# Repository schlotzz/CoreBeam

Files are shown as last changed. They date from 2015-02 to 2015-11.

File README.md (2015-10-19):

CoreBeam Logo

CoreBeam is a low cost DIY laser cutter/engraver based on [CoreXY](http://corexy.com/) kinematics. Its size can be scaled easily to suit your requirements and without the need to reprint parts.

### CoreBeam Key Features
- low cost, entry-level solution
- easy to build and assemble with basic hobbyist tools
- workspace size can be increased easily

### What electronics/firmware have been used?
The machine is controlled by a [slightly modified](https://github.com/schlotzz/grbl) version 0.9i of [grbl](https://github.com/grbl/grbl) running on an Arduino Uno with grbl-shield, a custom hand-soldered MOSFET-PCB and a cheap current limiting circuit-board.

### Which software can I use?
Due to using grbl as firmware a wide range of software can be used with CoreBeam. For streaming g-code via USB both [Universal G-Code Sender](https://github.com/winder/Universal-G-Code-Sender) and [GrblController](https://github.com/zapmaker/GrblHoming) have been tested successfully. Designing vector-images and converting them into g-code is easy as pie with [InkScape](https://inkscape.org) and the [LaserEngraver](http://www.slackersdelight.com/instructables/laserengraver.zip) extension, a heavily modified version of [Gcodetools](http://www.cnc-club.ru/forum/viewtopic.php?f=15&p=101).

### What materials can be handled?
Using a 2W 445nm M140 blue laser diode, CoreBeam has been tested for working with the following materials:

| Material | Cut | Engrave |
| :--- | :---: | :---: |
| Paper (any color) | Yes | Yes |
| Cardboard (any color) | Yes | Yes |
| Corrugated cardboard | Yes | Yes |
| Foam rubber (Polyurathane) | Yes | Yes |
| Synthetic felt | Yes | Yes |
| Wood (<= 1mm) | Yes | Yes |
| Wood (> 1mm) | No | Yes |
| Leather (<= 3mm) | Yes | Yes |
| Self-adhesive foils | Yes | Yes |
| Acrylic | No | Yes |
| Metal | No | No |

### Safety warnings
A powerfull laser diode is **not a toy**. Focused laser beams can burn your skin and damage your eyes permanently if not used responsibly. Please do yourself a favor and always use suitable, **certified laser goggles** while working with your laser cutter/engraver.
I do recommend operating CoreBeam only in well ventilated areas and only on materials **not emitting toxic fumes**.

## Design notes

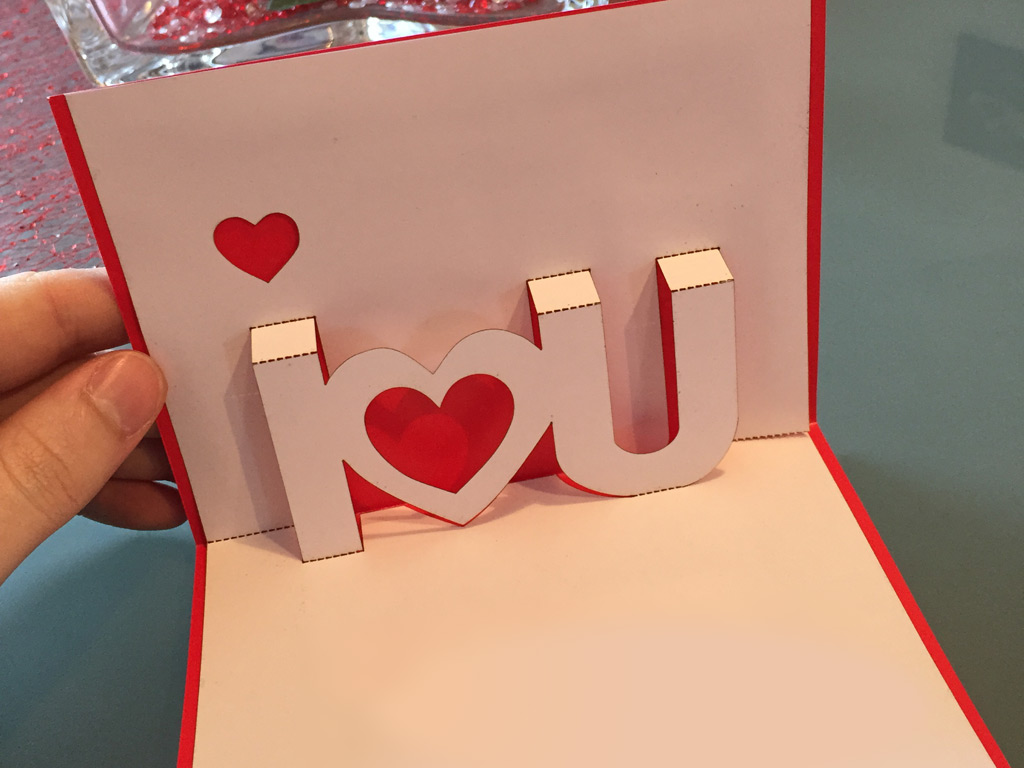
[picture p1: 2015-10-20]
media/materials/paper-cut.jpg

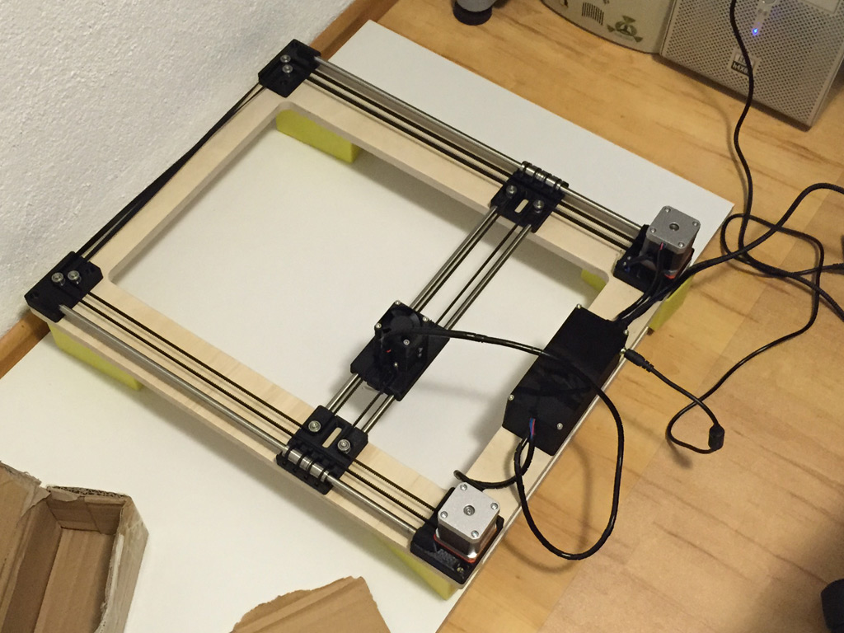
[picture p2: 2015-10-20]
media/buildlog/electronics-enclosed.jpg

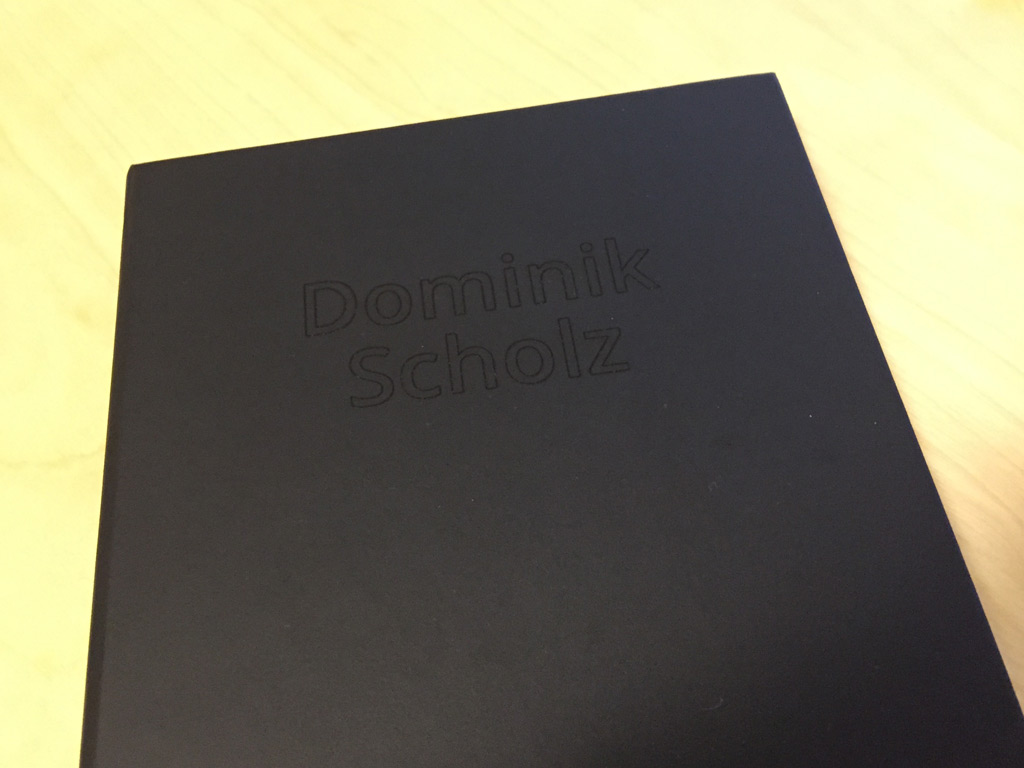
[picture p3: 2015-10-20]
media/materials/paper-book-engraved.jpg

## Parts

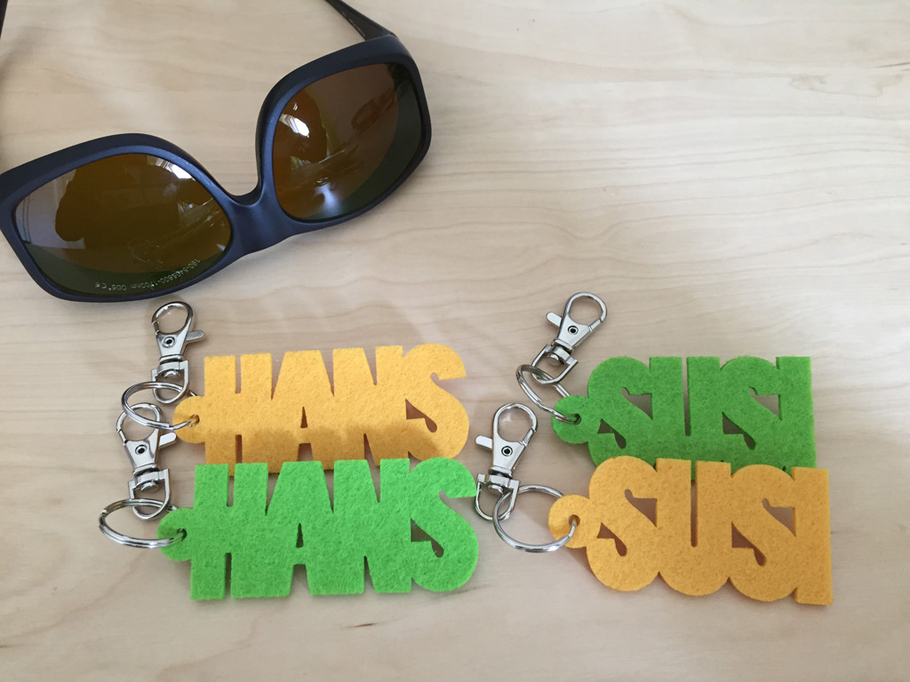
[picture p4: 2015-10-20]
media/materials/synthetic-felt-cut.jpg

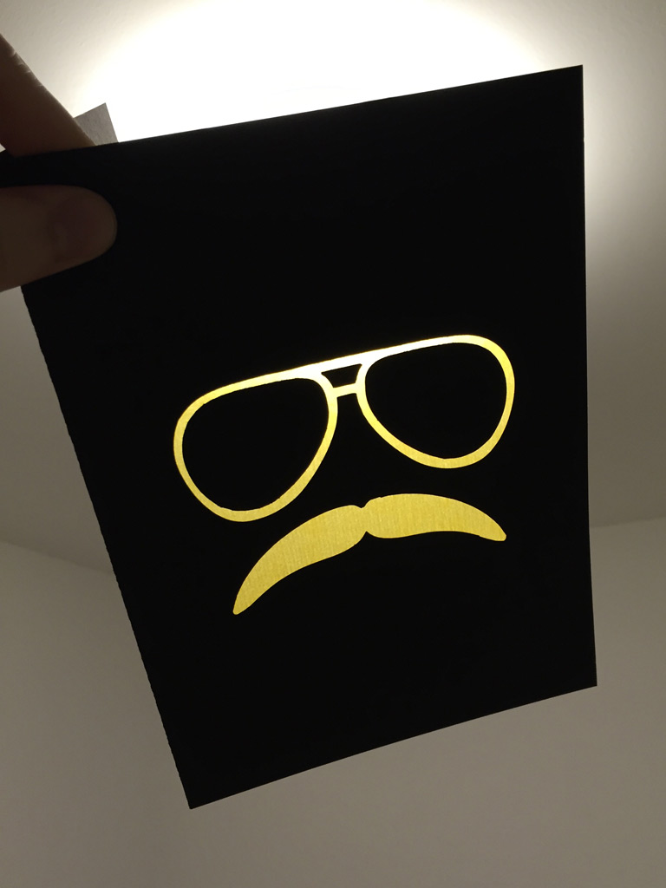
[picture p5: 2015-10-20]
media/materials/cardboard-cut.jpg

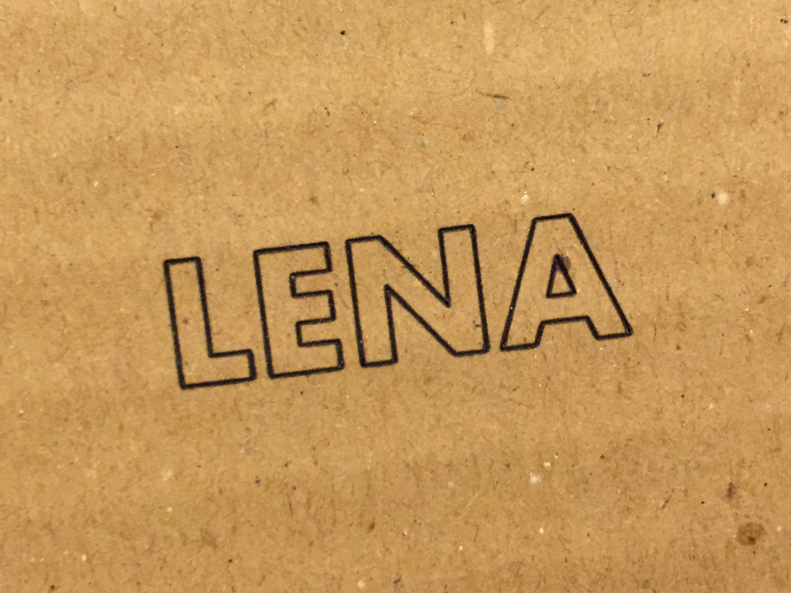
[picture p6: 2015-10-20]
media/materials/corrugated-cardboard-engraved.jpg

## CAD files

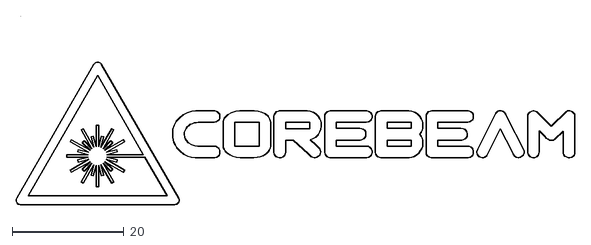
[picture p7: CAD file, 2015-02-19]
logo/corebeam.dxf
100.0 x 33.7

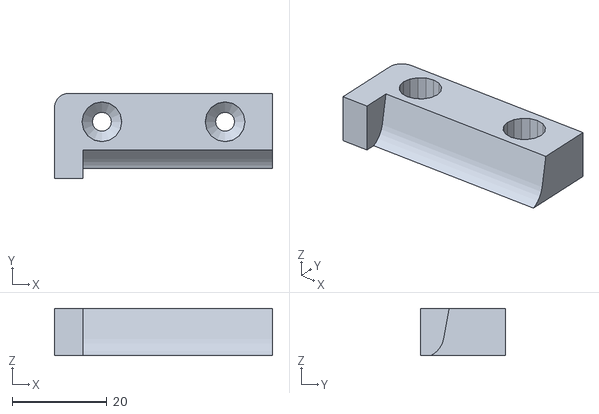
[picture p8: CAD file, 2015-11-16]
stl/pedestal-stopper.stl
46.0 x 18.0 x 10.0

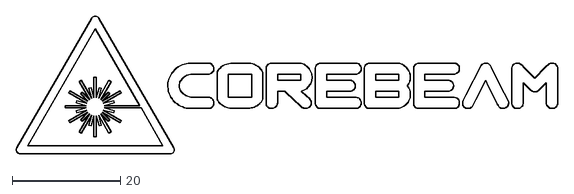
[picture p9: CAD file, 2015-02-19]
logo/corebeam-simplified-foreground.dxf
100.0 x 25.5

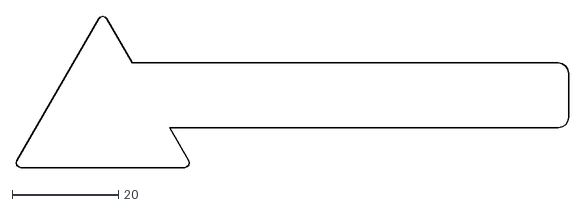
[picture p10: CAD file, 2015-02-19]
logo/corebeam-simplified-background.dxf
104.0 x 28.4

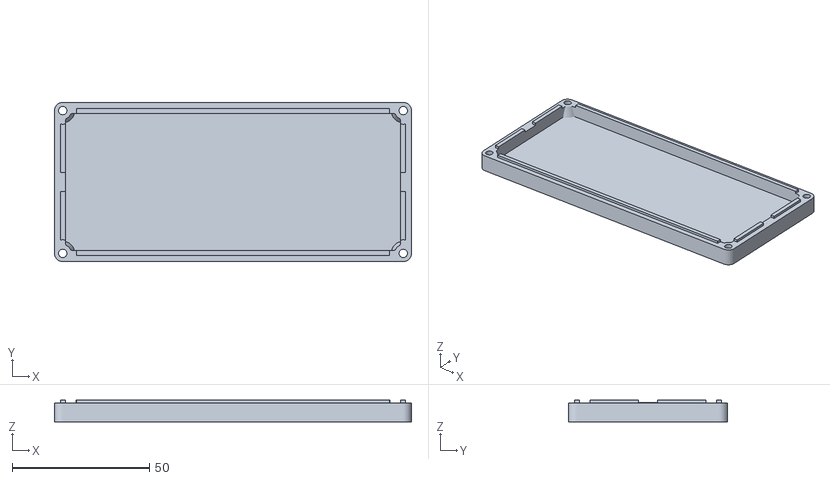
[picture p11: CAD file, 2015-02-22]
stl/electronics-case-lid.stl
130.0 x 58.0 x 8.00

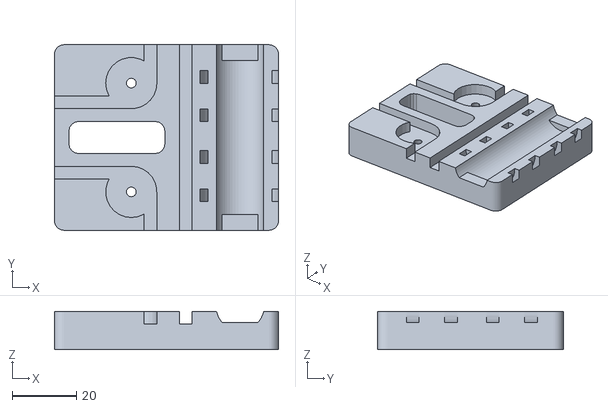
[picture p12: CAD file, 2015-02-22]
stl/stage-y.stl
70.0 x 58.0 x 12.0

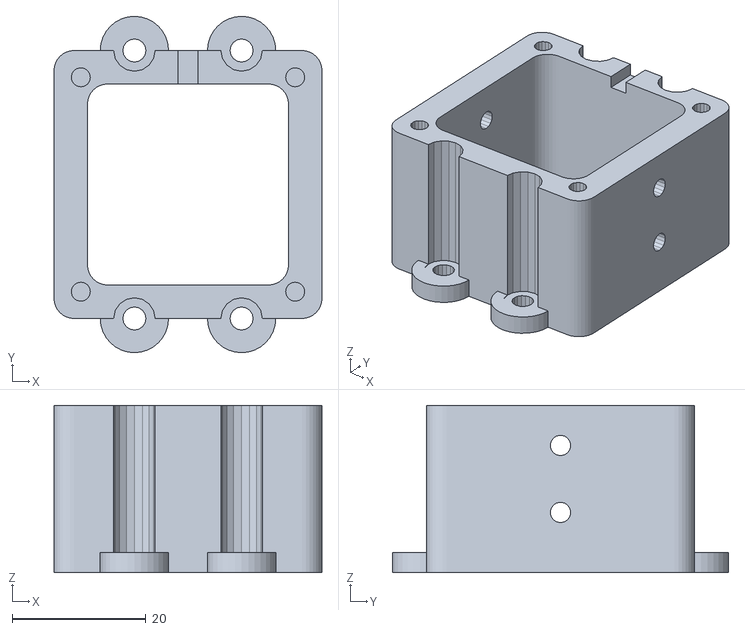
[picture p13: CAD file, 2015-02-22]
stl/laser-tower.stl
40.0 x 50.2 x 25.0

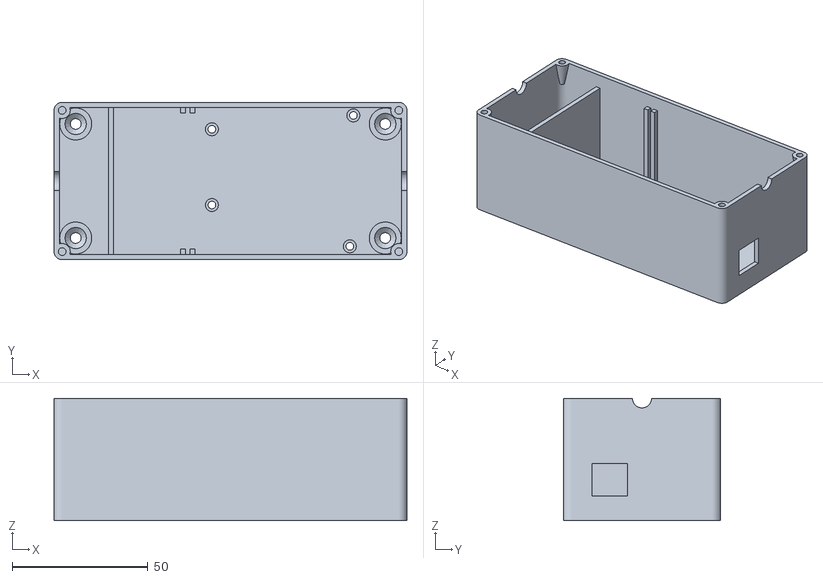
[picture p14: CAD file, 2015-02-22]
stl/electronics-case.stl
130.0 x 58.0 x 45.0

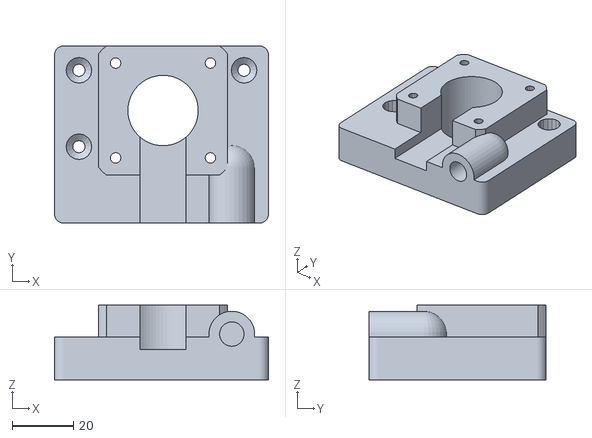
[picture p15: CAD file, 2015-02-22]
stl/stage-bottom.stl
70.0 x 58.0 x 24.5

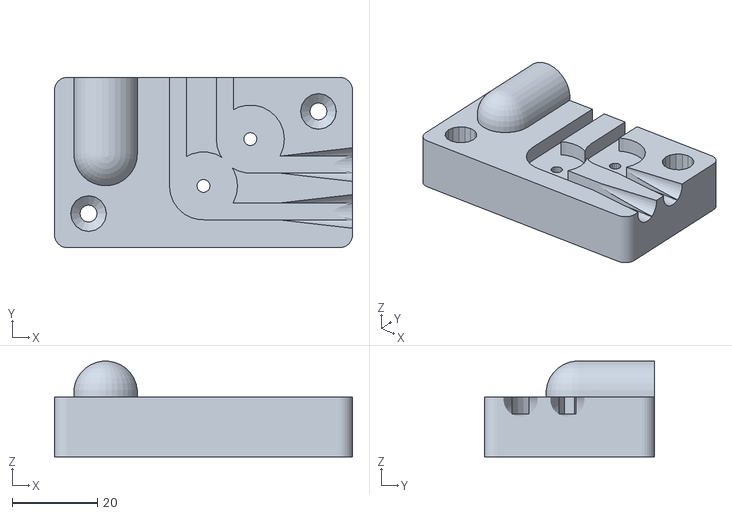
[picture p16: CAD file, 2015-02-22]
stl/stage-top-mirrored.stl
70.0 x 40.0 x 22.5

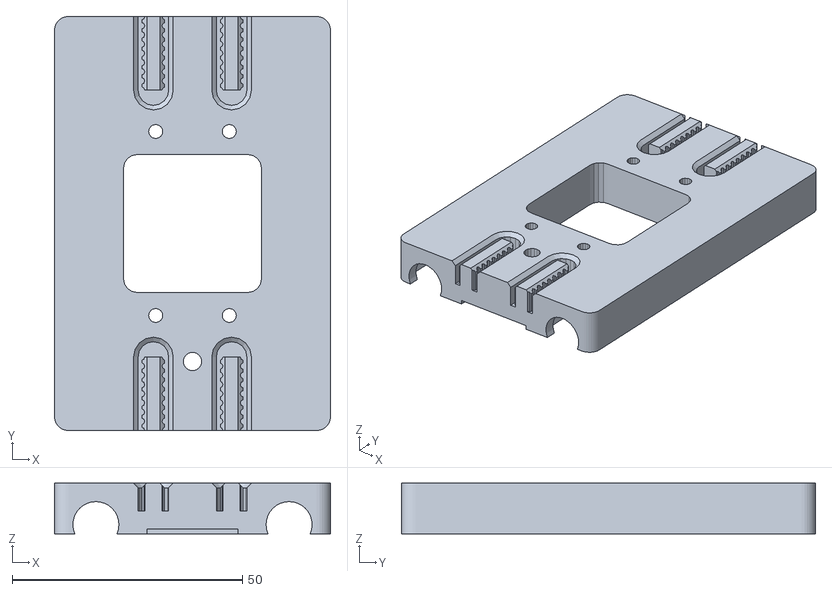
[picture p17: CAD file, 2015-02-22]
stl/stage-x.stl
60.0 x 90.0 x 11.0

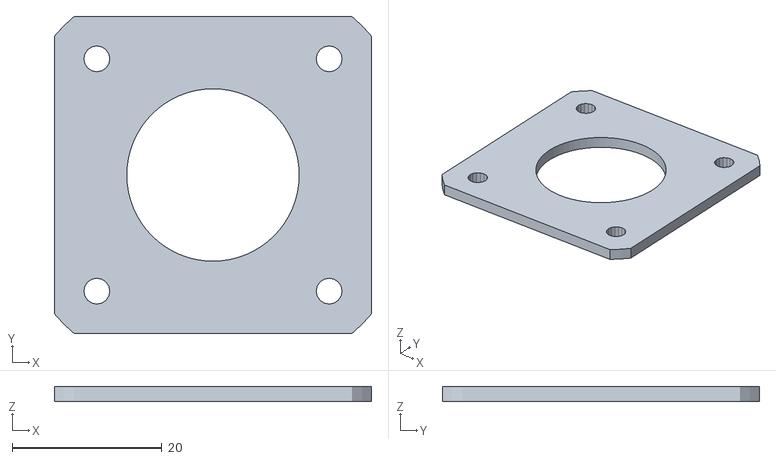
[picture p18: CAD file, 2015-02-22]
stl/motor-shim.stl
42.3 x 42.3 x 2.00

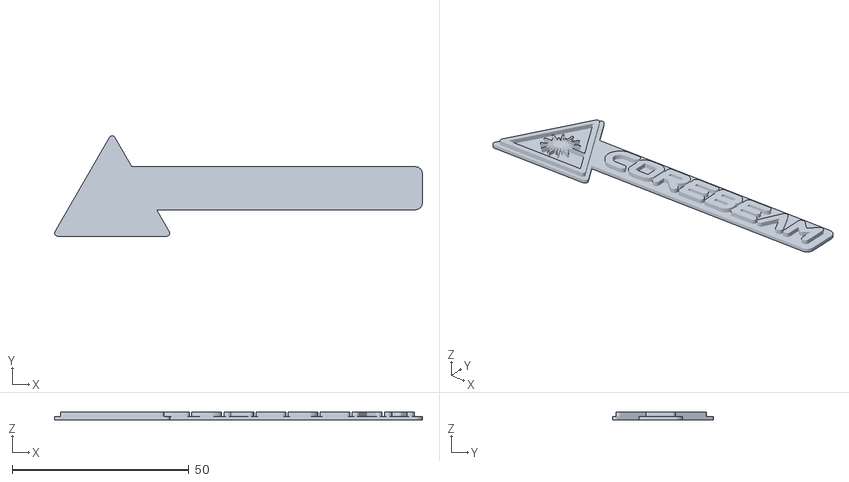
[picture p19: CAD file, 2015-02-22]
stl/corebeam-label.stl
104.0 x 28.4 x 2.25

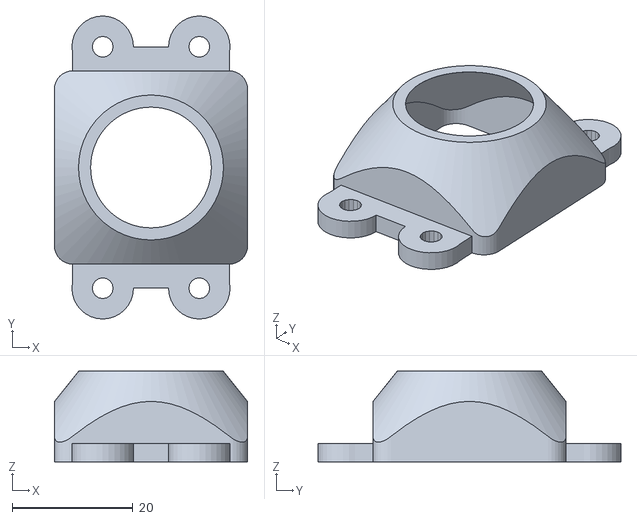
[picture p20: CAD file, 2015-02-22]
stl/laser-end-cap.stl
32.0 x 50.2 x 15.0

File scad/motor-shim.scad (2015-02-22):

// CoreBeam Laser Engraver
//
// Licence: CC BY-SA 3.0, http://creativecommons.org/licenses/by-sa/3.0/
// Author: Dominik Scholz <schlotzz@schlotzz.com>
// visit: http://www.schlotzz.com
//
// bottom motor mount shim


// include files
include <common.scad>;



// motor shim
module bottom_stage_motor_shim()
{
	depth = 2;

	difference()
	{
	
		intersection()
		{
			translate([0, 0, depth / 2])
				cube([nema17_width, nema17_width, depth], center = true);
			cylinder(r = nema17_width / 2 + 7, h = depth, $fn = 64);
		}

		// nema17 holes
		translate([0, 0, -epsilon])
		union()
		{
			// mounting holes
			for (i = nema17_hole_offsets)
				translate(i)
					cylinder(r = m3_wide_radius, h = 30, $fn = 16);

			// center cutout for pulley
			cylinder(r = 11 + 0.5, h = depth + 2 * epsilon, $fn = 64);

			// cutout for belt
			//translate([-7.5, -50, 0])
			//	cube([15, 50, depth + 2 * epsilon]);
		}
	}
}

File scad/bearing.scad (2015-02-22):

// CoreBeam Laser Engraver
//
// Licence: CC BY-SA 3.0, http://creativecommons.org/licenses/by-sa/3.0/
// Author: Dominik Scholz <schlotzz@schlotzz.com>
// visit: http://www.schlotzz.com
//
// several bearings and holders


// include files
include <common.scad>;



// lm8uu bearing
module bearing_lm8uu(bearings)
{
	bearing_diameter = 15;
	bearing_length = 24 + .1;

	rotate([90, 0, 0])
		difference()
		{
			cylinder(r = bearing_diameter / 2, h = bearing_length * bearings, $fn = 32, center = true);
			cylinder(r = 8 / 2, h = bearing_length * bearings + 2 * epsilon, $fn = 16, center = true);
		}
}

// cutouts for lm8uu linear bearing with zipties
// Author: Dominik Scholz <schlotzz@schlotzz.com>
// original author: Josef Průša <iam@josefprusa.cz> and contributors
module bearing_cutout_lm8uu(bearings = 1)
{
	// dimensions
	bearing_diameter = 15;
	bearing_length = 24 + .1;
	cutter_length = 10 + bearings * bearing_length;
	one_holder_length = 8 + bearing_length;
	holder_length = 8 + bearings * bearing_length;
 
	// main bearing cut
	difference()
	{
		translate([0, 0, 12 + 1.5])
			rotate([90, 0, 0])
				translate([0, 0, -cutter_length / 2])
					cylinder(h = cutter_length, r = bearing_diameter / 2, $fn = 50);

		// bearing retainers
		translate([0, 1 - holder_length / 2, 3 + 1.5])
			cube([24, 6, 8], center = true);
		translate([0, -1 + holder_length / 2, 3 + 1.5])
			cube([24, 6, 8], center = true);
	}
 
	// ziptie cutouts
	for (i = [0 : bearings - 1])
	{
		translate([0, -holder_length / 2, 0])
		{
			translate([0, one_holder_length / 2 + i * 25,0])
			{
				difference()
				{
					union()
					{
						translate([0, 2 - 6, 12])
							rotate([90, 0, 0])
								cylinder(h = 4, r = 12.5, $fn = 50);
						translate([0, 2 + 6, 12])
							rotate([90, 0, 0])
								cylinder(h = 4, r = 12.5, $fn = 50);
  					}
					
					translate([0, 10, 12])
						rotate([90, 0, 0])
							cylinder(h = 24, r = 10, $fn = 50);
				}
			}
		}
	}

	// show bearing
	%translate([0, 0, 13])
		bearing_lm8uu(bearings);
}



// cutouts for lm8uu linear bearing
module bearing_cutout_lm8uu_simple(bearings = 1)
{
	// dimensions
	bearing_diameter = 15;
	bearing_length = 24 + .5;
	cutter_length = bearing_length * bearings;
 
	// main bearing cut
	rotate([90, 0, 0])
		cylinder(h = cutter_length, r = bearing_diameter / 2, center = true, $fn = 50);
 
	// show bearing
	%bearing_lm8uu(bearings);
}


// 2x623zz flanged bearing (3x10x4mm) as belt idler pulley
module bearing_623zz_pulley()
{
	// dimensions
	bearing_inner_diameter = 10;
	bearing_outer_diameter = 11.5;
	bearing_inner_height = 3;
	bearing_outer_height = 1;
	bearing_height = bearing_inner_height + bearing_outer_height;
	bearing_hole_diameter = 3;

	difference()
	{
		union()
		{
			// inner cylinder
			cylinder(r = bearing_inner_diameter / 2, h = bearing_height * 2, $fn = 32);
			
			// flanges
			for (z = [0, bearing_height * 2 - bearing_outer_height])
				translate([0, 0, z])
					cylinder(r = bearing_outer_diameter / 2, h = bearing_outer_height, $fn = 32);
		}

		// inner mounting hole
		translate([0, 0, -epsilon])
			cylinder(r = bearing_hole_diameter / 2, h = bearing_height * 2 + epsilon * 2, $fn = 16);
	}

}


// cutout for 623zz bearing pulley including belt path
module bearing_cutout_623zz_pulley()
{
	bearing_outer_diameter = 11.5 + 4.5;
	bearing_inner_height = 3;
	bearing_outer_height = 1;
	bearing_height = bearing_inner_height + bearing_outer_height;
	bearing_hole_diameter = 3;
	screw_length = 16;
	belt_width = 4;
	belt_length = 40;

	union()
	{
		// main body cutout
		translate([0, 0, screw_length - bearing_height * 2])
			cylinder(r = bearing_outer_diameter / 2, h = bearing_height * 2);
		
		// mounting hole for screw
		cylinder(r = m3_radius, h = screw_length, $fn = 16);

		// hexnut retaining hole
		translate([0, 0, -epsilon - 10])
			m3_hexnut_cutout(epsilon + 10);

		// belt path
		translate([bearing_outer_diameter / 2 - belt_width, 0, screw_length - bearing_height * 2])
			cube([belt_width, belt_length, bearing_height * 2]);
		translate([-belt_length, -bearing_outer_diameter / 2, screw_length - bearing_height * 2])
			cube([belt_length, belt_width, bearing_height * 2]);
	}

	// show idler pulleys
	%translate([0, 0, 8])
		bearing_623zz_pulley();
}


// belt path
module belt_path(length = 100)
{
	bearing_inner_height = 3;
	bearing_outer_height = 1;
	bearing_height = bearing_inner_height + bearing_outer_height;
	screw_length = 16;
	belt_width = 4;

	translate([0, -length / 2, screw_length - bearing_height * 2])
		cube([belt_width, length, bearing_height * 2]);
}

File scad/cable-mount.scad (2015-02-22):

// CoreBeam Laser Engraver
//
// Licence: CC BY-SA 3.0, http://creativecommons.org/licenses/by-sa/3.0/
// Author: Dominik Scholz <schlotzz@schlotzz.com>
// visit: http://www.schlotzz.com
//
// cable mount


// include files
include <common.scad>;



// cable mount for holding stepper motor cables on wooden frame
module cable_mount()
{
	depth = 10;
	height = 5;
	radius = 7 / 2;
	thickness = 4;
	wings = 9;

	difference()
	{
		// base
		union()
		{
			intersection()
			{
				translate([0, radius, 0])
					cylinder(r = radius + thickness, h = depth, $fn = 64);
				translate([-radius - thickness, 0, 0])
					cube([2 * radius + 2 * thickness, 2 * radius + thickness, depth]);
			}
			translate([-radius - thickness - wings, 0, 0])
				cube([2 * radius + 2 * thickness + 2 * wings, height, depth]);
		}
	
		// cable cutout
		translate([0, radius, -epsilon])
			cylinder(r = radius, h = depth + 2 * epsilon, $fn = 32);
		translate([-radius, -epsilon, -epsilon])
			cube([radius * 2, radius + epsilon, depth + 2 * epsilon]);

		// mounting holes
		for (i = [-radius - thickness - wings + 5, radius + thickness + wings - 5])
		translate([i, 0, depth / 2])
			rotate([-90, 0, 0])
				woodscrew_cutout();
	}
}

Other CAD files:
stl/pedestal-stopper-mirrored.stl
stl/stage-top.stl
stl/pedestal.stl
stl/laser-holder.stl
scad/common.scad
scad/corebeam-label.scad
scad/electronics-case-lid.scad
scad/electronics-case.scad
scad/gt2-belt.scad
scad/laser-end-cap.scad
scad/laser-holder.scad
scad/laser-metal-case.scad
scad/laser-tower.scad
scad/pedestal-stopper.scad
scad/pedestal.scad
scad/stage-bottom.scad
scad/stage-top.scad
scad/stage-x.scad
scad/stage-y.scad
scad/switch.scad
stl/arduino-uno.stl
stl/cable-mount.stl
stl/stage-bottom-mirrored.stl

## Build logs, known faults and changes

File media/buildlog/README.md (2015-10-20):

### CoreBeam assembly

Having printed all plastic parts and cut all smooth rods to length, assembling the CoreBeam laser cutter isn't that hard. I made some photos over the build process to show several milestones, but some photos of details are missing and are only mentioned in the text.

### X-Axis
1. Take the short smooth rods and slide two LM8UU linear bearings on each of it.
2. Put the x stage onto the four bearings. It will snap on easily.
3. Slide the y stages onto the ends of the smooth rods.
4. Insert another two LM8UU linear bearings into each y stage and secure them with zip ties. Place the zip tie ends on top of each y stage to avoid later problems.
5. Mount four 623zz bearings on each y stage as pulley. Insert a M3 spacer on the mounting hole. Place two bearings with the brim on the outside on top and secure them with a M3 screw. Use a M3 hexnut in the hexnut trap on the bottom of the stage.

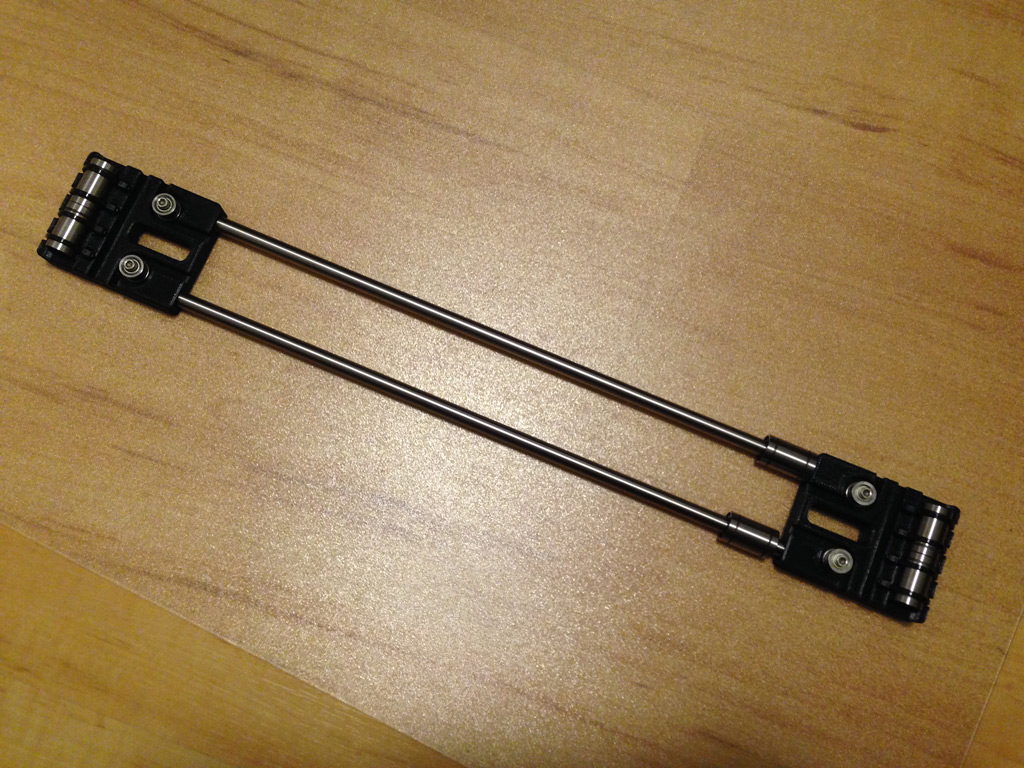
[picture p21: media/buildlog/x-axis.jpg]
photo of x-axis, missing two linear bearings

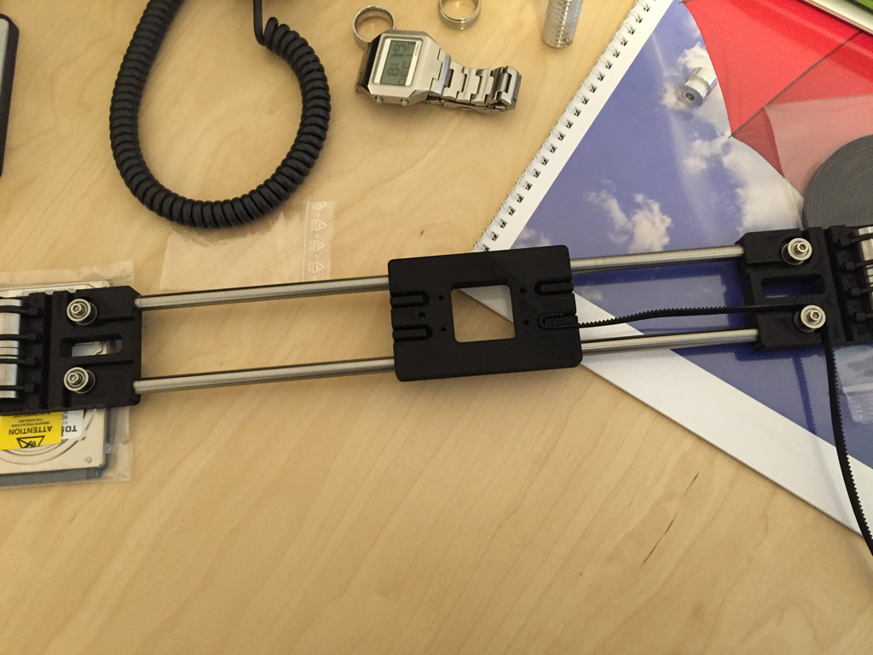
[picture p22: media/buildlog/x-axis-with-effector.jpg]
photo of x-axis with effector attached


### Y-Axis
1. Mount the NEMA17 stepper motors with the GT2 pulleys attached on their correlating plastic parts, the wires pointing to the inner side. Maybe you need to insert a spacer, if the shaft of your motor is too long and will exceed the height of the plastic mount.
2. Mount four 623zz bearings on each top corner as pulley. Insert a M3 spacer on the mounting hole. Place two bearings with the brim on the outside on top and secure them with a M3 screw. Use a M3 hexnut in the hexnut trap on the bottom of the stage.
3. Insert the long smooth rods into the bottom corner with your stepper motors. Slide the previous built x-axis onto it. Now attach the top corners.

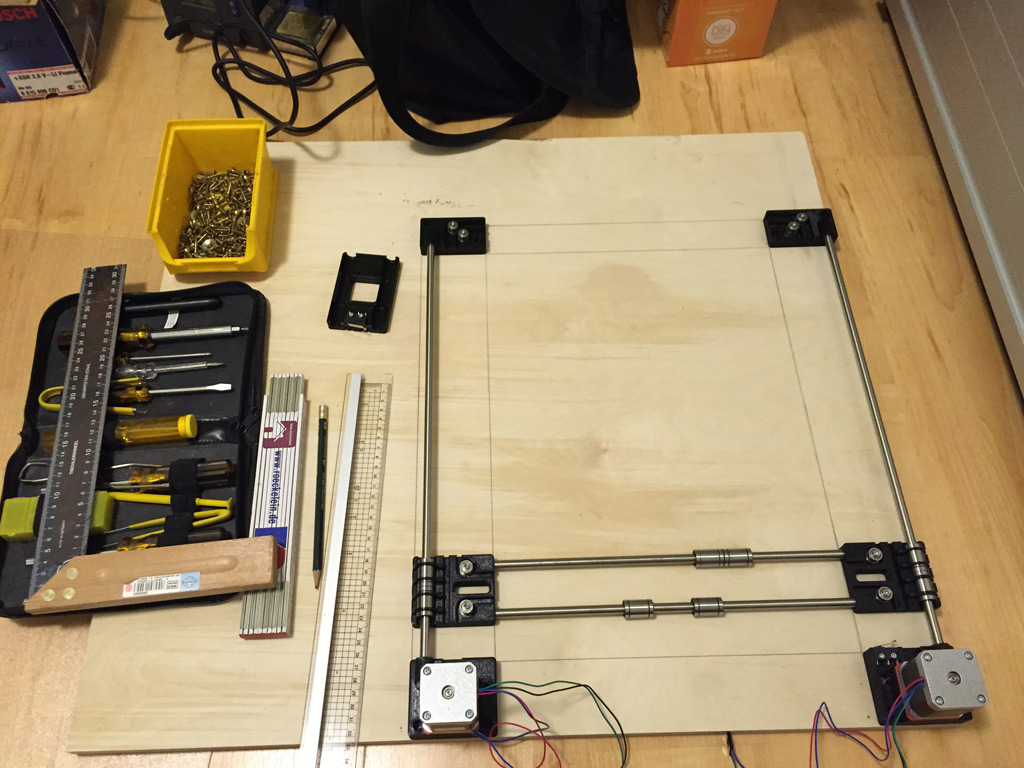
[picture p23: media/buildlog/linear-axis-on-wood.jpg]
photo of y-axis, x-axis attached


### Wooden frame
1. Place the linear-rails onto the wood. Use pencil and ruler to mark the dimensions of your build and the holes for the wood screws.
2. Use a drill to cut holes in each inner corner. I used a 20mm diameter forstner drill to make nice looking rounded corners.
3. Cut the wood with jig saw too size.
4. Use a small drill to pre-drill the mounting holes on the frame.
5. Mount the corners onto the frame using two wood screws on each corner.

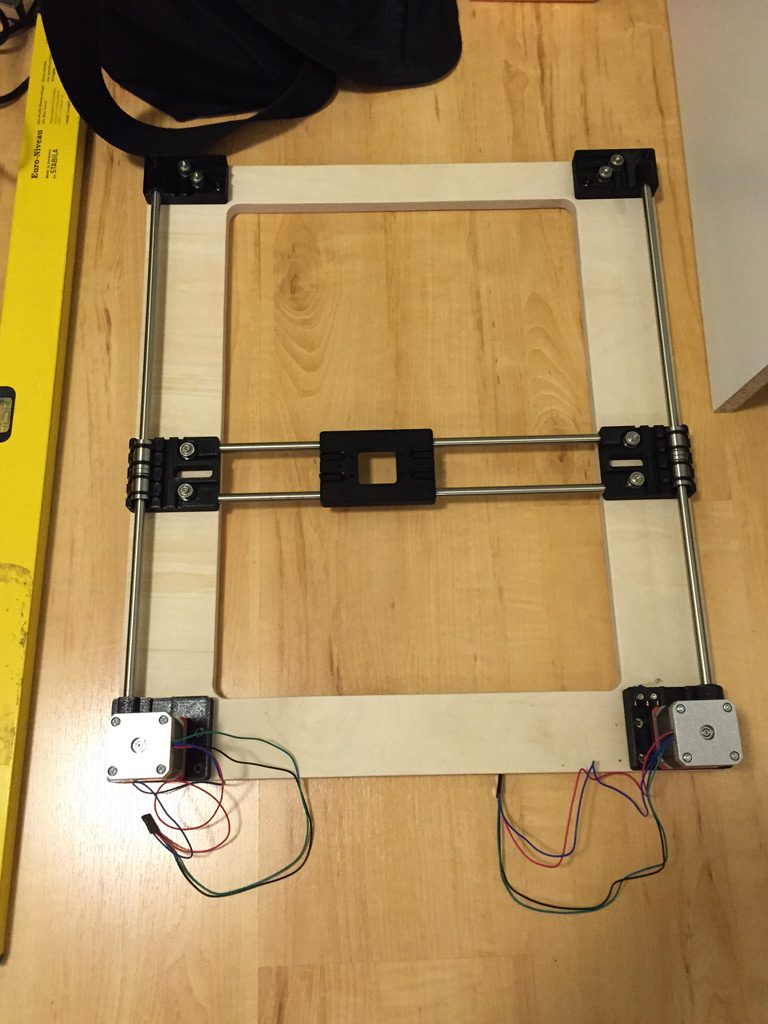
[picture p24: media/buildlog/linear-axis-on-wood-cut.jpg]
photo of wooden frame with linear rails attached


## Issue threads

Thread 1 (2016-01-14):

laser cutter project

splitn2, 2016-01-14:
Hi, I have a spare Raspberry Pi and already a GRBL on Uno and 3 axis 8825 shield, and motors, so I am keen to trial this laser cutter. I was interested in what is the difference between your GRBL variant and the standard? I am running GRBL 0.9J at the moment with UGS 2.0 on the Raspberry Pi. Do you have a schematic of the electronics you used? What laser did you end up going with? Thanks heaps I hope you don;t mind me pestering you. cheers, Richard

schlotzz, 2016-01-16:
Hi splitn2. Nice to hear that you'll give CoreBeam a try.
The difference between the official and my branch of GRBL are some bugfixes in the CoreXY kinematics homing algorithm, that haven't been merged to master, yet. I'm using UniversalGcodeSender with no problems on my Raspberry PI for controlling my laser, too.
It's a pity but I haven't made any documentations on the electronics, yet. Basically it's the Arduino UNO with GRBL shield / A4988 stepper drivers and a small selfmade MOSFET board to drive the fan / laser diode driverboard with corresponding pins on the GRBL shield. For the laser diode a small current limiting board of a chinese ebay vendor was used, but I'm going to replace it with a cheap TTL laser driver soon.
As laser a blue 445nm laser diode is used. I took a M140 2W+ laser diode with housing and G2 lens. It performs quite well, even if it's driven below 2W.

Please feel free to ask whenever you need more information on building your CoreBeam.
I'm looking forward to seeing a new build ;-)

Regards,
Dominik

These are some parts needed for electronics:
- new TTL laser driver: http://www.ebay.de/itm/281836302983
- GRBL shield with A4988 stepper drivers http://www.ebay.de/itm/321873677496
- blue laser diode 445nm 2W+ with housing and G2 lens http://www.ebay.de/itm/180948106909

splitn2, 2016-01-16:
Hi Dominic, thanks very much for responding, very appreciated.

I’ll press on with my CoreBeam build once I get another larger CNC project out of the way. I am almost finished building a large very heavy duty steel xyz router, with MACH3 control. When I have that running some of the smaller projects will be customized machines running specific jobs for engraving and cutting soft materials.

So much fun these projects eh!!!!!

Cheers

Rich

many thanks

Richard Harcourt

Ph +64-3-3266585

sales@splitn2.com

SPLITN2.COM <http://www.splitn2.com/>

Splitboarding Equipment Specialist New Zealand

WWW.WHITEDOTSKIS.CO.NZ

Whitedot Skis New Zealand

splitn2_outlook_signature_logo

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

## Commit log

2015-02-19 Initial upload of project on GitHub
    [arduino-uno.stl, bearing.scad, cable-mount.scad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]
2015-02-22 Cleaned up some OpenSCAD files, re-rendered STLs
    Did some clean-up of OpenSCAD files, did some minor bug-fixes, exported
    STLs
    [bearing.scad, cable-mount.scad, corebeam-label.scad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]
2015-10-19 Updated Readme, link to custom grbl version
2015-11-14 Added pedestal-stopper, updated .gitignore
    New part for building a footer plate
    [pedestal-stopper-mirrored.stl, pedestal-stopper.scad, pedestal-stopper.stl]
2015-11-16 Updated pedestal-stopper, now with rounded edge
    Mounting the pedestal stoppers onto wood looks strange, if edges are not
    rounded properly...
    [pedestal-stopper-mirrored.stl, pedestal-stopper.scad, pedestal-stopper.stl]
